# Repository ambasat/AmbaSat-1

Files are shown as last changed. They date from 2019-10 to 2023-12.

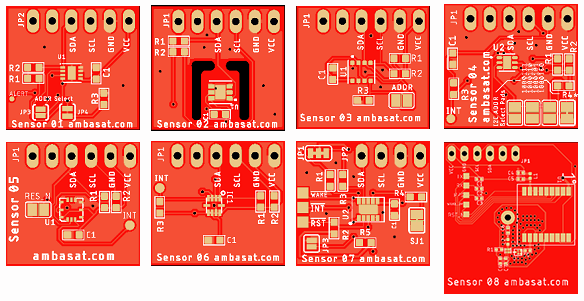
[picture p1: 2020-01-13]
Eagle/Daughterboards/AmbaSat-1-Sensor-range.png

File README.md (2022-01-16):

# AmbaSat-1

[Learn more at ambasat.com](https://ambasat.com)



AmbaSat-1 is tiny spacecraft kit that you assemble and code yourself.

Once your satellite kit is assembled and programmed, it will be launched onboard a commercial rocket which will deploy your satellite into Low Earth Orbit, where it will spend up to 3 months in space.

AmbaSat-1 is part of a new generation of satellites known as Sprite satellites. They are tiny spacecraft measuring 35 mm square and just a few millimetres thick. Pioneered by the original KickSat, groups of AmbaSat-1 satellites are launched onboard a commercial rocket. By shrinking the spacecraft, up to 200 satellites can be launched at a time, reducing costs.

Making use of The Things Network (TTN), AmbaSats are capable of transmitting data to over seven thousand earthbased TTN receivers (Gateways) which are spread around the whole globe. No specialist radio receiving equipment is required, your data appears over the internet directly to your AmbaSat Dashboard.

AmbaSats are just a little bigger than the size of a couple of postage stamps but have solar cells, a LoRaWAN radio transceiver, microcontroller (an Arduino compatible ATMEGA 328P-AU), memory, a gyroscope, accelerometer, magnetometer as well as a range of other sensor options. 

What’s in the AmbaSat Kit?

1. AmbaSat PCB – the main board where all the components are placed, including the MCU (Micro Controller Unit)
2. Micro Controller Unit – the brains of AmbaSat. This is where your code lives
3. Solar Panels – Spaceflight approved solar panels providing power to your satellite
4. Transceiver – The radio communications chip. This is the chip which will send data back to Earth and into your AmbaSat Dashboard
5. FTDI board – this is used for coding and converts your USB port to serial
6. Gyroscope, Accelerometer, Magnetometer – used to locate your satellite in space
7. A bag of parts containing resistors, capacitors, voltage regulator and other components
8. Your chosen sensor 

Software Coding (Programming the Satellite)

AmbaSat-1 is fully Arduino compatible and code is written using C/C++

Whether you’re new to the ‘C’ language or a seasoned pro, we have all the libraries, example source code and interfaces you need to get your satellite flying.

The AmbaSat kit comes complete with a FTDI USB adapter allowing direct coding in the Arduino IDE (based on C/C++). It’s the most popular programming environment for makers and hardware enthusiasts. 
AmbaSat is fully compatible with all Arduino related code examples. That’s because your satellite uses the well-respected Atmel ATMEGA-328 which is exactly the same microprocessor used by Arduino. In fact, your satellite is compatible with all online Arduino software libraries and your code will work with Arduino shields and modules with little or no library code modifications.

Never coded before? Don’t know the first thing about hardware?
That’s no problem. The AmbaSat Kit build will take you from learning how to use a soldering iron all the way through to assembling and coding your very own satellite. We’ve created a detailed step-by-step learning process:

Step 1. Unpacking your kit: What’s inside. The basics

Step 2. Electronics basics: Resistors, capacitors, MCU and other components

Step 3. Your toolbox: What you need. How to use it

Step 4. Assembly: The hardware and PCB. Putting it together

Step 5. Introduction to coding: Welcome to Arduino (C/C++). Let’s get your satellite coded

Step 6. Your AmbaSat Dashboard: Connecting to your Dashboard. Sending data from your satellite

What can I do with my satellite?
Measure! Explore! Measure!

What better way of showing off your uber-cool geekness than building your own spacecraft?

Your AmbaSat is fun but it’s also practical. Maybe you’re just looking to put your very own spacecraft into space. That’s great and also very cool. You can program it to send any message back to Earth that you like. However, if you’re looking for practical applications, including studying the environmental impact of gases, radiation, global warming, etc then read on!

Every AmbaSat comes loaded with a gyroscope, accelerometer and magnetometer sensor. These sensors come in the form of an integrated chip (IC) which is called the LSM9DS1. In low Earth orbit, there is no GPS signal available so this chip helps plot your satellite’s orbit in space. It’s a versatile, motion-sensing system-on-a-chip. It houses a 3-axis accelerometer, 3-axis gyroscope, and 3-axis
magnetometer – nine degrees of freedom (9DOF) in a single IC. See the LSM9DS1 overview section for more details on what this fantastic IC can do. In addition to the LSM9DS1, when you select your AmbaSat kit, you get the option to choose which type of additional sensor you would like to fit onto your satellite.

AmbaSat is Open Source
We’ve learned a lot from the open source community. Electronics, hardware, coding, software libraries and much more.

So, we want to give our work back to the maker and open source community.

The AmbaSat satellite software is fully open-source and available for full download. The AmbaSat satellite hardware is also totally open source and the schematics and Bill of Materials (BoM) are available for download.

What this means is that you can fully use all the above and create your own version of the AmbaSat satellite. Go ahead and use the schematic and source code and create your very own space satellite.

Come and join the journey at ambasat.com

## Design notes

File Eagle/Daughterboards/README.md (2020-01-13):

AmbaSat-1 sensors come on 'daughterboards' which you solder to the main AmbaSat-1 printed circuit board (PCB).

<!-- wp:heading -->
<h2>Available Sensor Options</h2>
<!-- /wp:heading -->

<!-- wp:paragraph -->
<p>There are eight sensors choices available, shown in the list below. One daughterboard sensor can fit on a single AmbaSat-1 mainboard.  </p>
<!-- /wp:paragraph -->

<h2>Sensor Boards</h2>



<!-- wp:paragraph -->
<p><strong>Sensor 01:    SHT30-DIS-F2.5KS  </strong></p>
<!-- /wp:paragraph -->

<!-- wp:paragraph -->
<p>Humidity and Temperature - Best in class Humidity &amp; Temperature Sensor. Fully calibrated, linearized, and temperature compensated digital output with a wide supply voltage range, I2C Interface with communication speeds up to 1MHz and two user selectable addresses.  Typical accuracy of 1.5 %RH and 0.1 °C. Very fast start-up and measurement time. All in a tiny 8-Pin DFN package.</p>
<!-- /wp:paragraph -->

<!-- wp:paragraph -->
<p><strong>Sensor 02    STS21   </strong></p>
<!-- /wp:paragraph -->

<!-- wp:paragraph -->
<p>Temperature - A 3x3mm, fully calibrated digital temperature sensor with impressive performance. The temperature sensor features a I²C address and comes with outstanding accuracy and low power consumption. </p>
<!-- /wp:paragraph -->

<!-- wp:paragraph -->
<p><strong>Sensor 03    BME680  </strong></p>
<!-- /wp:paragraph -->

<!-- wp:paragraph -->
<p>Gas, Pressure, Temp &amp; Humidity - a low power gas, pressure, temperature &amp; humidity sensor. It is a 4-in-1 multi-functional MEMS environmental sensor which integrates VOC (Volatile Organic Compounds) sensor, temperature sensor, humidity sensor and barometer. Monitor 4 environmental parameters simultaneously. Widely used in environmental monitoring, home automation and control, Internet of Things (IoT) wearable device, GPS, etc.</p>
<!-- /wp:paragraph -->

<!-- wp:paragraph -->
<p><strong>Sensor 04 OPT3001 DNPT  </strong>  </p>
<!-- /wp:paragraph -->

<!-- wp:paragraph -->
<p>Ambient Light Sensor - The OPT3001 is a sensor that measures the intensity of visible light. The spectral response of the sensor closely matches the photopic response of the human eye, with infrared rejection. It is a single-chip lux meter, measuring the intensity of light as visible by the human eye. The precision spectral response and strong IR rejection of the device enables the OPT3001 to accurately meter the intensity of light as seen by the human eye regardless of light source.</p>
<!-- /wp:paragraph -->

<!-- wp:paragraph -->
<p><strong>Sensor 05    ZMOD44 10AI1V   TVOC (Total Volatile Organic Compounds)</strong></p>
<!-- /wp:paragraph -->

<!-- wp:paragraph -->
<p>Designed for detecting total volatile organic compounds (TVOC). The ZMOD4410 is a 12-pin LGA assembly (3.0 x 3.0 x 0.7 mm) that consists of a gas sense element and a CMOS signal conditioning IC. The module’s sense element consists of heater element on a Si-based MEMS structure and a metal oxide (MOx) chemiresistor. The signal conditioner controls the sensor temperature and measures the MOx conductivity, which is a function of the gas concentration.</p>
<!-- /wp:paragraph -->

<!-- wp:paragraph -->
<p><strong>Sensor 06    SI1132-A10-GMR  UV Sensor </strong></p>
<!-- /wp:paragraph -->

<!-- wp:paragraph -->
<p>The Si1132 is a low-power, ultraviolet (UV) index, and ambient light sensor with I2C digital interface and programmable-event interrupt output. This sensor IC includes an analog-to-digital converter, integrated high sensitivity visible and infrared photodiodes, and digital signal processor. The Si1132 offers excellent performance under a wide dynamic range and a variety of light sources including direct sunlight.</p>
<!-- /wp:paragraph -->

<!-- wp:paragraph -->
<p><strong>Sensor 07    CCS811B-JOPD500 TVOC &amp; CO2 </strong></p>
<!-- /wp:paragraph -->

<!-- wp:paragraph -->
<p>The CCS811 is an ultra-low power digital gas sensor solution which integrates a metal oxide (MOX) gas sensor to detect a wide range of Volatile Organic Compounds (VOCs) and includes an Analog-to-Digital converter (ADC), and an I²C interface. Supporting intelligent algorithms to process raw sensor measurements and output equivalent total VOC (eTVOC) and<br> equivalent CO2 (eCO2) values.</p>
<!-- /wp:paragraph -->

<!-- wp:paragraph -->
<p><strong>Sensor 08    TESEO-LIV3R*    GPS </strong></p>
<!-- /wp:paragraph -->

<!-- wp:paragraph -->
<p>The Teseo-LIV3R module is an easy to use Global Navigation Satellite System (GNSS) standalone positioning receiver IC working simultaneously on multiple constellations. This certified module comes with optimized RF, embedded firmware and is compact at only 9.7x10.1 mm. Supporting GPS, Glonass, BeiDou &amp; QZSS positioning systems.</p>
<!-- /wp:paragraph -->

<!-- wp:paragraph -->
<p><em>*Please note: Due to COCOM restrictions, the </em><em>TESEO GPS receiver will only work on Earth</em></p>
<!-- /wp:paragraph -->

<!-- wp:heading -->
<h2>Datasheets</h2>
<!-- /wp:heading -->

<!-- wp:paragraph -->
<p>Datasheets for each of the above sensors can be download
from the links at:</p>
<!-- /wp:paragraph -->

<!-- wp:heading -->
<h2><a href="https://ambasat.com/ambasat-2/sensor-options/">https://ambasat.com/ambasat-2/sensor-options/</a>&nbsp;</h2>
<!-- /wp:heading -->

<!-- wp:heading -->
<h2>Custom sensors</h2>
<!-- /wp:heading -->

<!-- wp:paragraph -->
<p>You can create a custom sensor as long as it conforms to
certain criteria, including size and safety. Your AmbaSat satellite provides
additional connectivity pins which expose the ATMEGA's I2C bus, as well as
digital and analogue pins, plus power. Please contact <a href="mailto:custom@ambasat.com">custom@ambasat.com</a> for more details.</p>
<!-- /wp:paragraph -->

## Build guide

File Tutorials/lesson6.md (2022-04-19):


## Introduction
Okay, you have got your Ambasat-1 board set up and also figured out how to transmit programs to the board using VSCode. Good job!

However... just running example programs is a bit boring. Let's do something more interesting; in this lesson, you will learn to use your imagination and create your very first satellite firmware.

## Requirements
 -  Ambasat-1 Satellite
 Ambasat-1 (https://ambasat.com/wp-content/uploads/2020/06/AmbaSat-1-Assembled-350.jpg "Ambasat-1")
 - USB programmer
 

In case you haven't set up your coding environment yet, you can complete this tutorial using the [Arduino Online Simulator](https://wokwi.com/projects/new/arduino-unohttp:// "Arduino Online Simulator")

## What is a program?

A program is a set of instructions that a computer follows in order to perform a particular task. There are multiple languages available to developers, each one of them is suited for specific applications. In the embedded field the most common languages used are C and C++. Other languages you may have heard of are **Python**, **Java**,, or **C#**. 

An Ambasat-1 source code or also called sketch( because of the Arduino framework) is composed of two main parts: setup code and a loop code.

### Setup  
- Executed immediately after power-up or reboot.
- It is where all the initializing code must be put, e.g., variables, pin modes, or libraries.

### Loop
- Executed after the setup function.
- Executed repeatedly, that is why the name 'Loop.'
- It is where the main task of the program gets executed.

### Example
```c
#include <Arduino.h>

// put your setup code here, to run once:
void setup() {
  Serial.begin(9800); // Initialize the Serial comunication, 9800 is the baudrate
  Serial.println("Setup code"); // Print the massage through the serial line
}

// put your main code here, to run repeatedly:
void loop() {
  Serial.println("loop code");
}
```
Let's try it yourself, copy and paste this code on  https://wokwi.com/projects/new/arduino-uno. Then, click the run button to start the simulation. What is the output?

As you can see, the line "Setup code" is printed only once at the begging. On the other hand, the line "loop code" is printed several times. Be aware that both functions setup() and loop() **MUST** be included in every program you write.

You have probably  noticed that the code has differen coloring and shading. These hints makes the code more easy to read and understand. Let's have a look at the main parts of the program.

To include a library, we use the keyword: `#include` followed by `<nameofthelibrary.h>`. In the example, we wrote `#include <Arduino.h>` to import the Arduino framework. Ignore for now what a framework is. Just think of it as the underlying layer that does the dirty work for us.

Notice that there are some plain English sentences in the code; those are called comments. We use comments to describe what the code is doing so that the other developers can understand more easily our code. We use a double slash followed by the comment itself to create a comment in C/C++.

    //This is a comment!

**Setup** and **Loop** are commonly called functions. You can think of functions as a collection of statements. We use a function to group statements together so that we can dynamically refer to them without having to rewrite them every time. Picture a function as a to-do list or a list of procedures that are executed in order.

    // put your main code here, to run repeatedly:
    void loop() {
      Serial.println("loop code");
    }
This one is a bit more complicated example. It looks scary, doesn't it? A function can optionally receive input values. In this case, *mysterious_fun* requires two numbers, **x** and **y**. Can you guess what the function does with these two parameters?

    void mysterious_fun( int x, int y)
    {
    	Serial.println(x+y);
    }

Try to execute the following code, what does it print?
    #include <Arduino.h>
    
    void setup() {
      // put your setup code here, to run once:
      Serial.begin(9800); // Initialize the Serial comunication, 9800 is the baudrate
      Serial.println("Setup code"); // Print the massage through the serial line
    }
    
    void loop() {
      // put your main code here, to run repeatedly:
      Serial.println("Hello");
      sum(5,2);
    }
    
    void mysterious_fun(int x, int y)
    {
      Serial.println(x+y);
    }

At this point, you might be asking yourself, "what is void?" Well, that is a fancy way of saying **nothing**. Technically it means that the function doesn't return anything. This implies that we can write a function that returns something, but that is a lesson for another day.
### Quiz Time

It is time to test what you have learned so far! (Don't worry, you won't be graded)

#### What is this line of code:
        // put your setup code here, to run once:
1. A keyword
2. A single line comment
3. A function definition
4. A cup of tea

#### What is this line of code 2:
    void loop() {
    	Serial.println("Hello Students!");
    }
1.  A statement
2.  A single line comment
3.  A function definition
4.  A banana

## Light the board up

Ok, now that you have a better understanding of what a program is, let's experiment with something more practical. In the following example, we are going to make our first LED blink! Don't worry, you don't need anything else than your Ambasat board. However, you can always spice things up and use an external Led along with the appropriate resistor.

### About LED
A light-emitting diode is an electronic component that emits light when current flows through it. It has two pins:
- Cathode (- pin) needs to be connected to GND (0V).
- Anode (+pin) is used to control LED status.

For most LEDS we must use a resistor to protect the LED. We place a resistor between the Anode (+) and the VCC(+5V). The value of the resistor depends on the specification of the LED. To control the status of the LED we connect the anode(+) to a digital pin so that we can dynamically change the pin output.

(https://i.ibb.co/sRKDYrF/Screenshot-2022-02-27-at-19-48-05.pnghttp://)
### Write the code
First, we must decide which digital pin we are going to use. For simplicity let's stick with the Ambasat onboard status LED which is connected to digital pin 9.
```c
#define INTERNAL_LED 9
```

Secondly, we must configure the pin status. There are two possible configurations; Input in case we are interested in reading the pin voltage; Output in case we are interested in controlling the pin output voltage. Obviously, we are interested in the latter, so we configure the INTERNAL_LED as Output:
```c
pinMode(INTERNAL_LED, OUTPUT);

```
Lastly, to control the LED status we use the following command
```c
digitalWrite(INTERNAL_LED, High or Low);
```
The following is an example of the LED blinking, try it yourself!
```c
#define LED 13

// put your setup code here, to run once
void setup() {
  // initialize digital pin LED as an output.
  pinMode(LED, OUTPUT);
}

// put your main code here, to run repeatedly:
void loop() {
  // turn the LED on (HIGH is the voltage level)
  digitalWrite(LED, HIGH);
  // wait for 1 second
  delay(1000);
  // turn the LED off by making the voltage LOW
  digitalWrite(LED, LOW);
  // wait for 1 second
  delay(1000);
}
```

 Now get you hands dirty, try to change the delay, what happened?
### Quiz Time 2
#### What does this line of code do:
       digitalWrite(LED, HIGH);
1. Digital write something
2. Turn the LED off
3. Reset the board 
4. Turn the LED on

#### What does this line of code do:
    delay(1000);
1.  Wait for 1000ms (1 second)
2.  Turn the LED on
3.  Write "hello" into the serial output
4.  Reset the board

### Exercise
Time to test your knowledge with some practical exercises! Try to complete as many as you can.

#### Change the example code so that the light is on for 500 milliseconds and off for 500 milliseconds. 

#### Change the example code so that the light is on for 50 milliseconds and off for 50 milliseconds. What happens?

#### Build a simple LED circuit and try to make this LED blink instead of the internal one. What line of code do you need to change?

#### Using the example code as a starting point, build a Blink SOS signal in Morse code.	
Tips:
- Morse code Alphabet is composed of just two basic signals - dots and dashes. The dot represents a quick and rapid signal. Dashes, on the other hand, represent a slow signal.
- SOS in Morse code is 3 dots - 3 dashes - 3 dots.
- How can we differentiate between dots and dashes with a LED? In a very simple way, by changing the time spent blinking.
- As general rule dashes should be three times longer than the dots.
- The timing between dots and dashes should be the length of a dot.
- To make the signal more clear, the pause between letters should be the same length as your dash blinks.

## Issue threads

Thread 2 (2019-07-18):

4Mhz Fuse Values

C4, 2019-07-18:
Hi, I was wondering what fuse values you were using to for the Atmega32P-AU chips before you install them on the boards? This would be nice to know for others that are building ambasat boards. Thanks!

ambasat, 2020-01-27:
Hi, here are the fuse values for 1MHz:

ambasatnode.menu.mhz.1MHz.bootloader.low_fuses=0x62
ambasatnode.bootloader.high_fuses=0xD6
ambasatnode.bootloader.extended_fuses=0x06

For 4MHz, change:

ambasatnode.menu.mhz.4MHz.bootloader.low_fuses=0x7D

Closed 2020-01-27.

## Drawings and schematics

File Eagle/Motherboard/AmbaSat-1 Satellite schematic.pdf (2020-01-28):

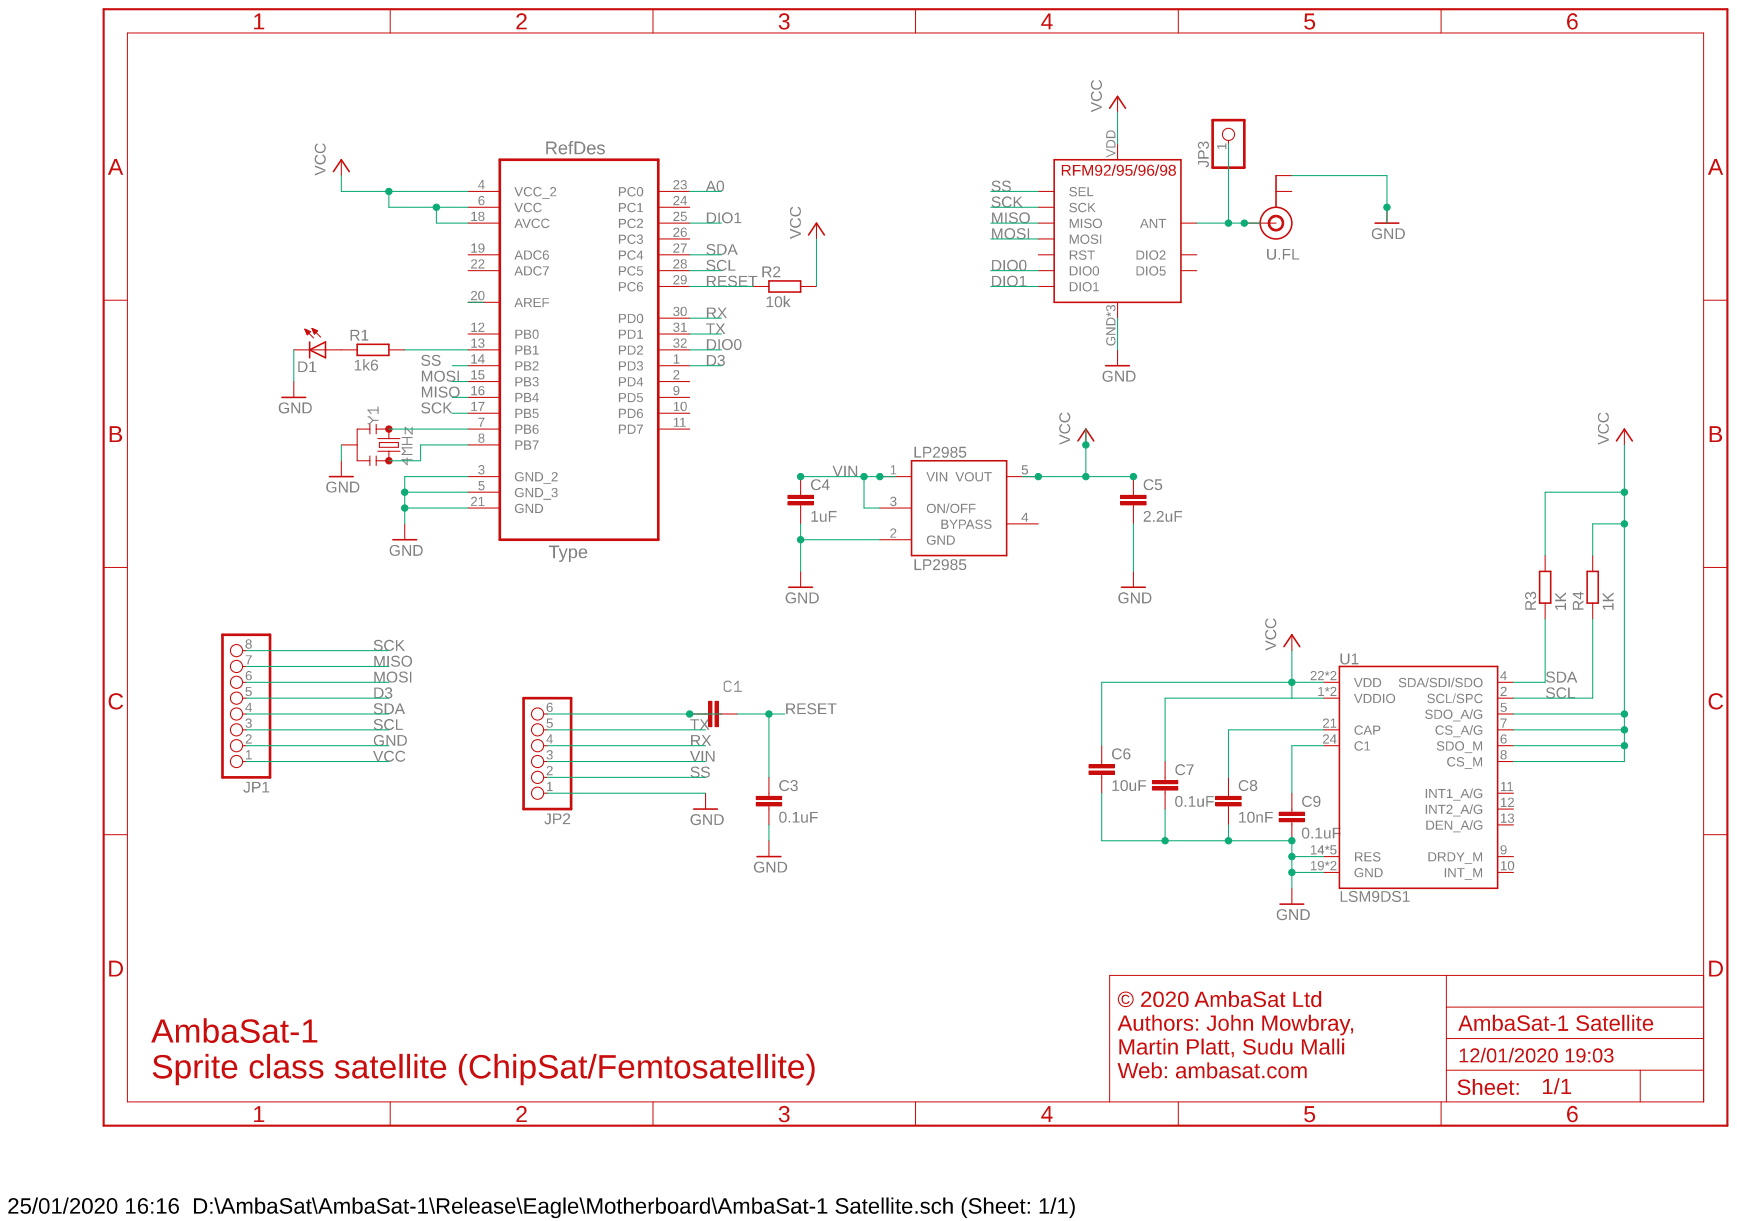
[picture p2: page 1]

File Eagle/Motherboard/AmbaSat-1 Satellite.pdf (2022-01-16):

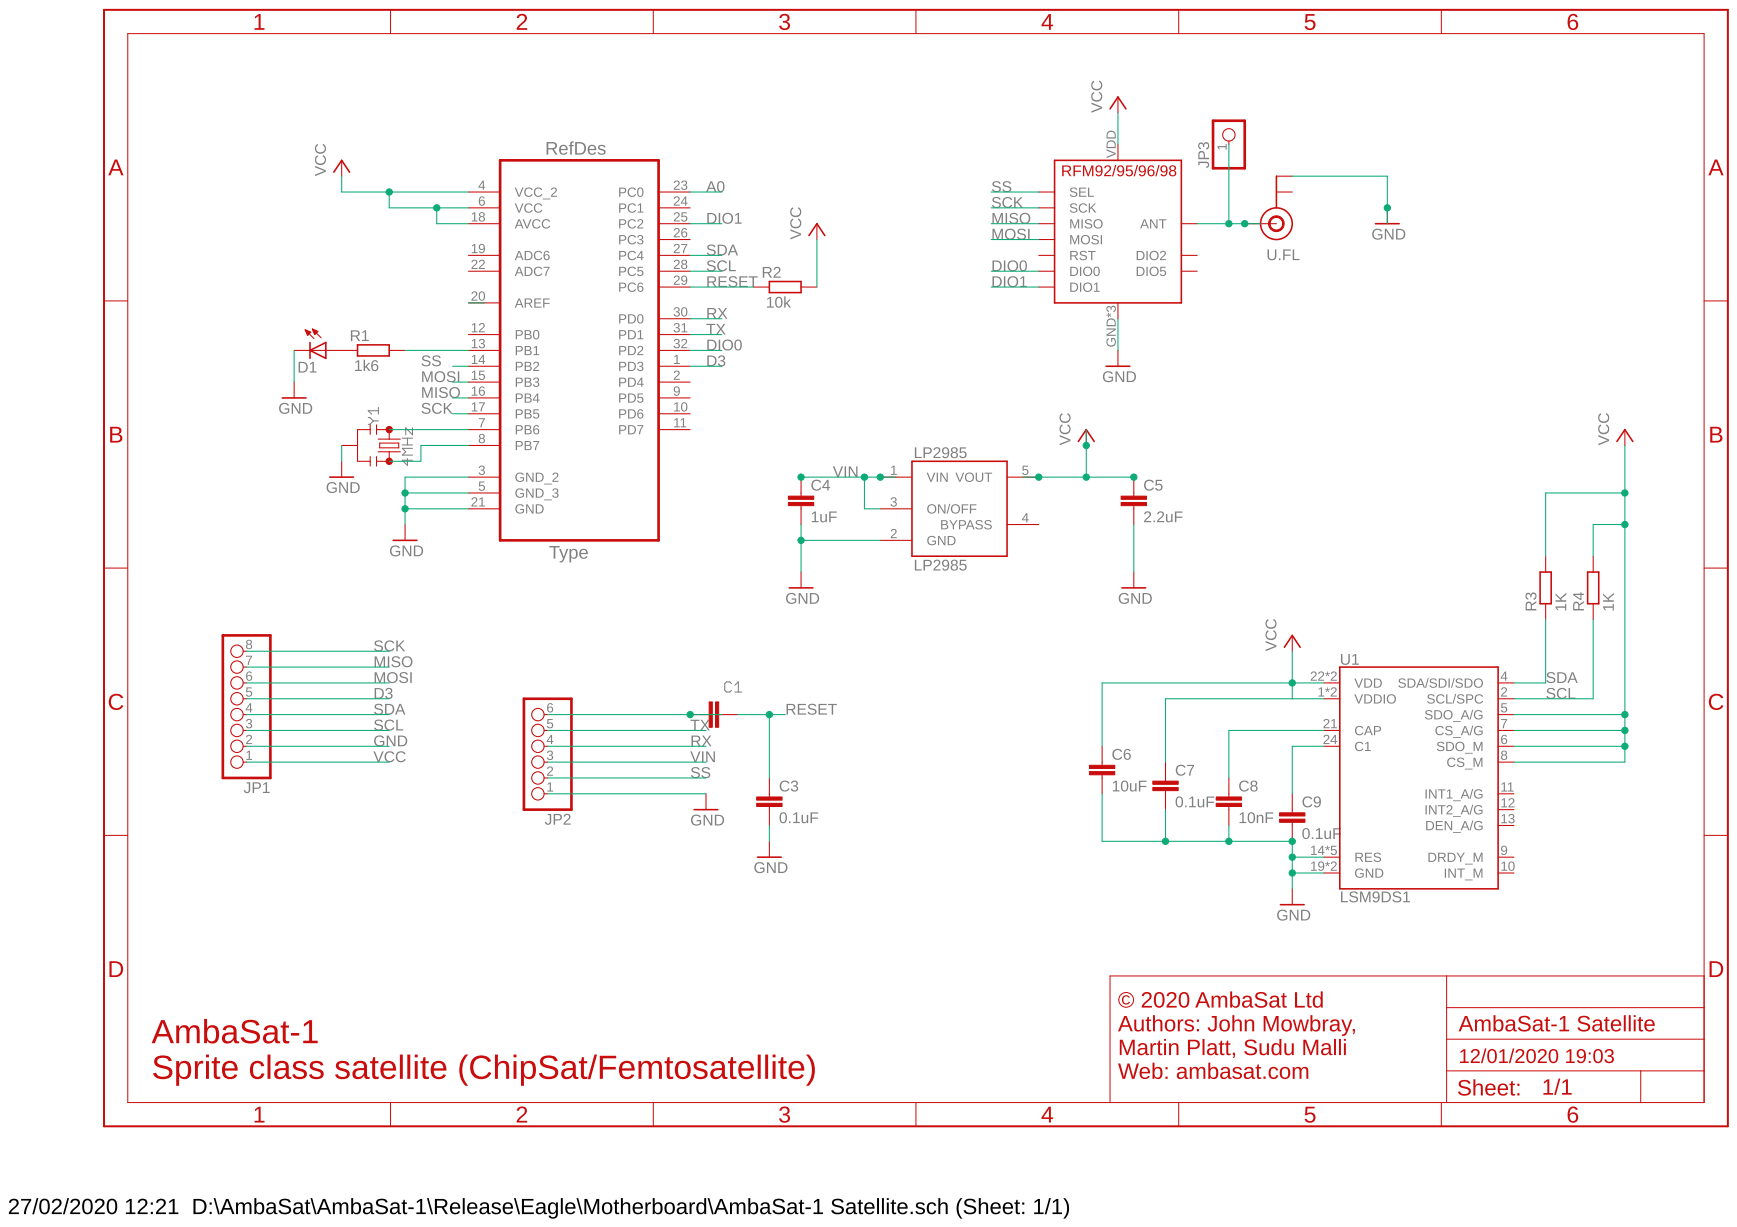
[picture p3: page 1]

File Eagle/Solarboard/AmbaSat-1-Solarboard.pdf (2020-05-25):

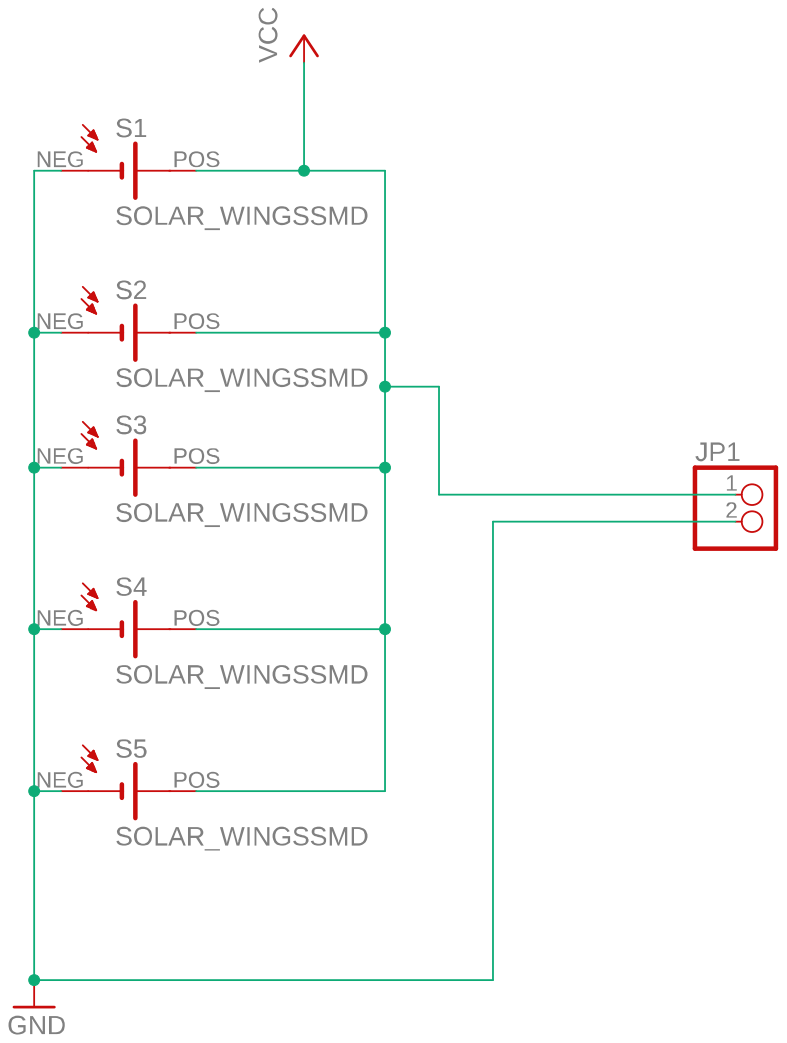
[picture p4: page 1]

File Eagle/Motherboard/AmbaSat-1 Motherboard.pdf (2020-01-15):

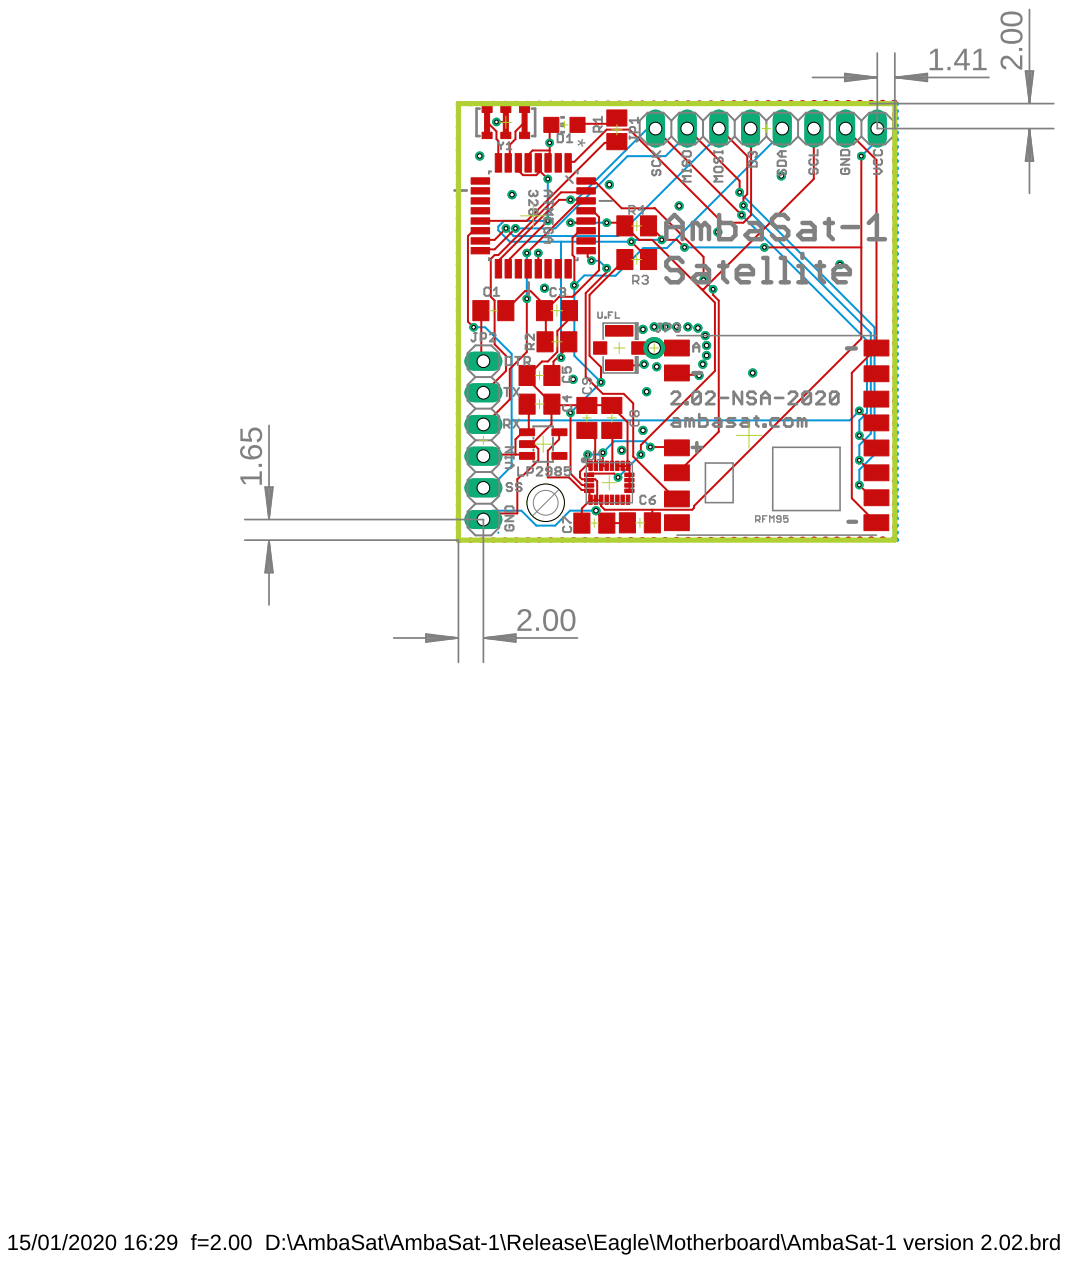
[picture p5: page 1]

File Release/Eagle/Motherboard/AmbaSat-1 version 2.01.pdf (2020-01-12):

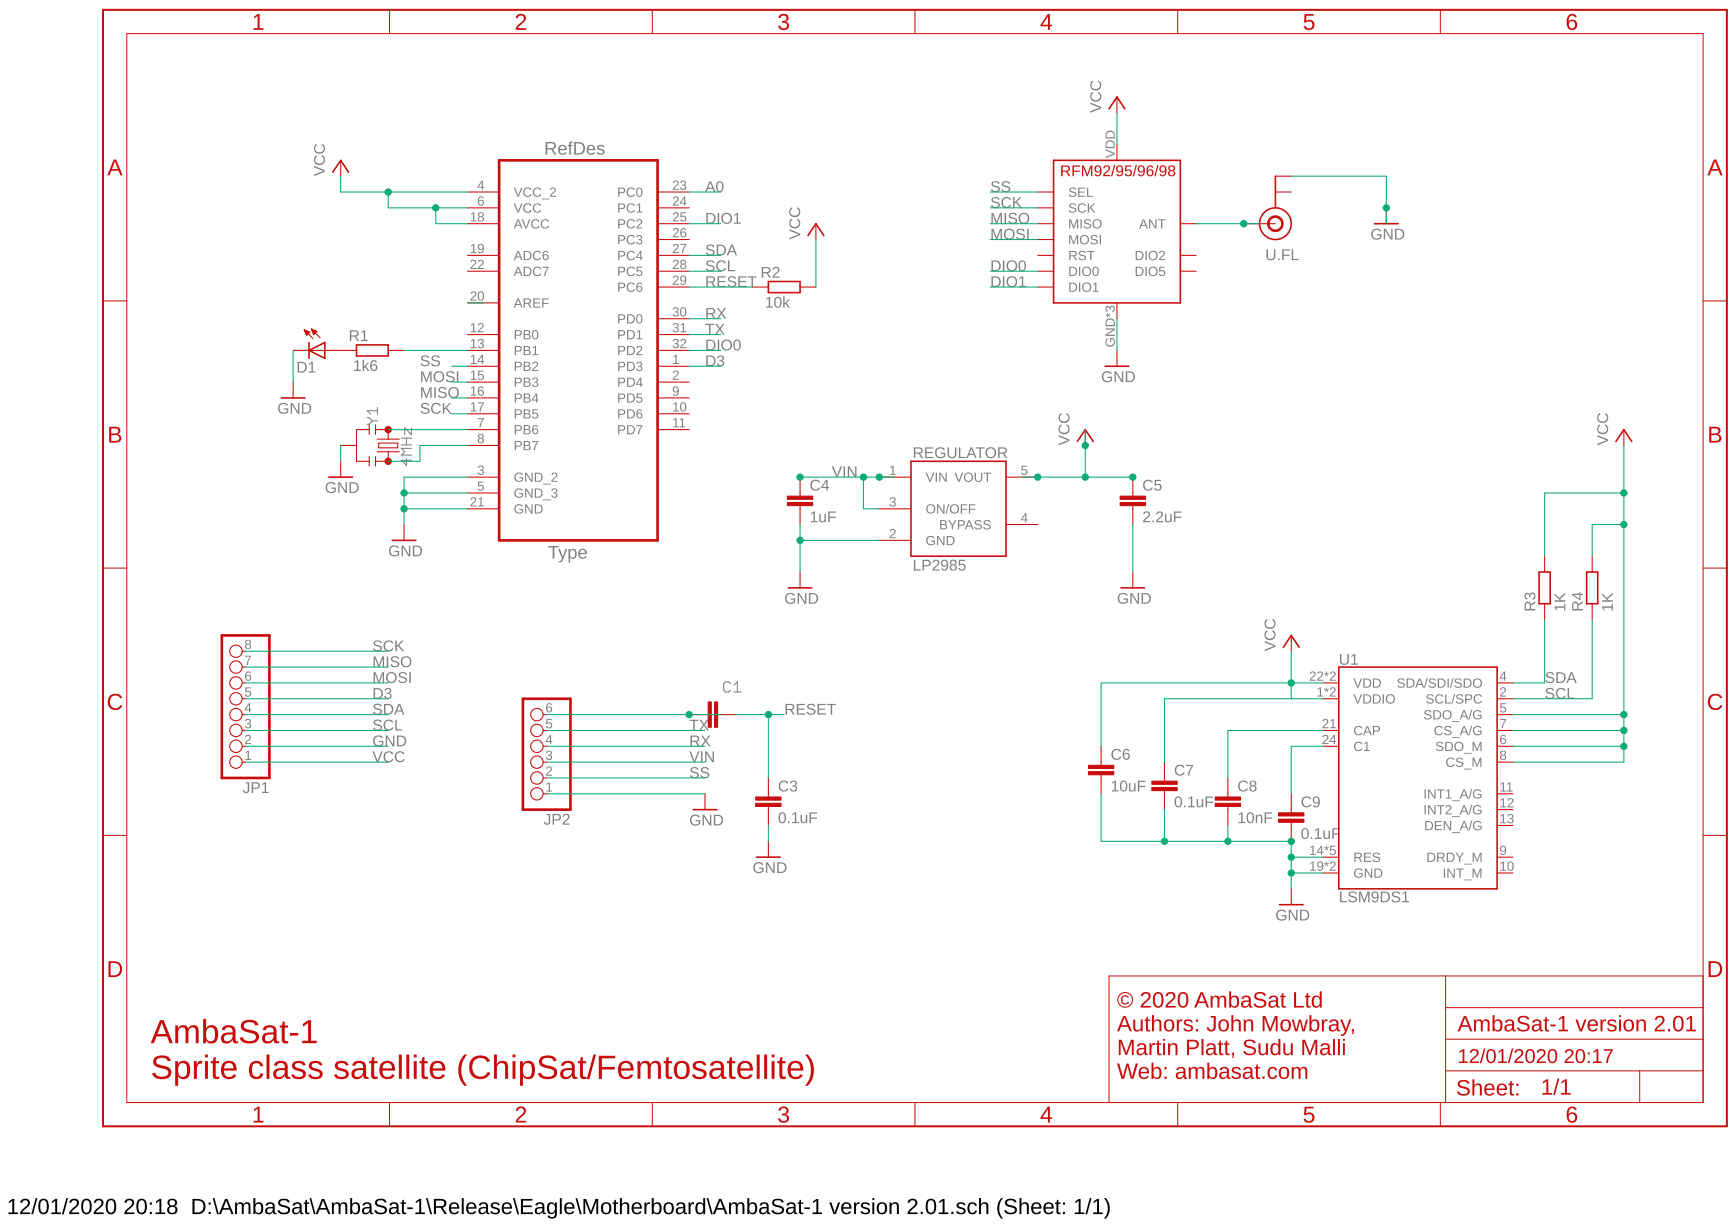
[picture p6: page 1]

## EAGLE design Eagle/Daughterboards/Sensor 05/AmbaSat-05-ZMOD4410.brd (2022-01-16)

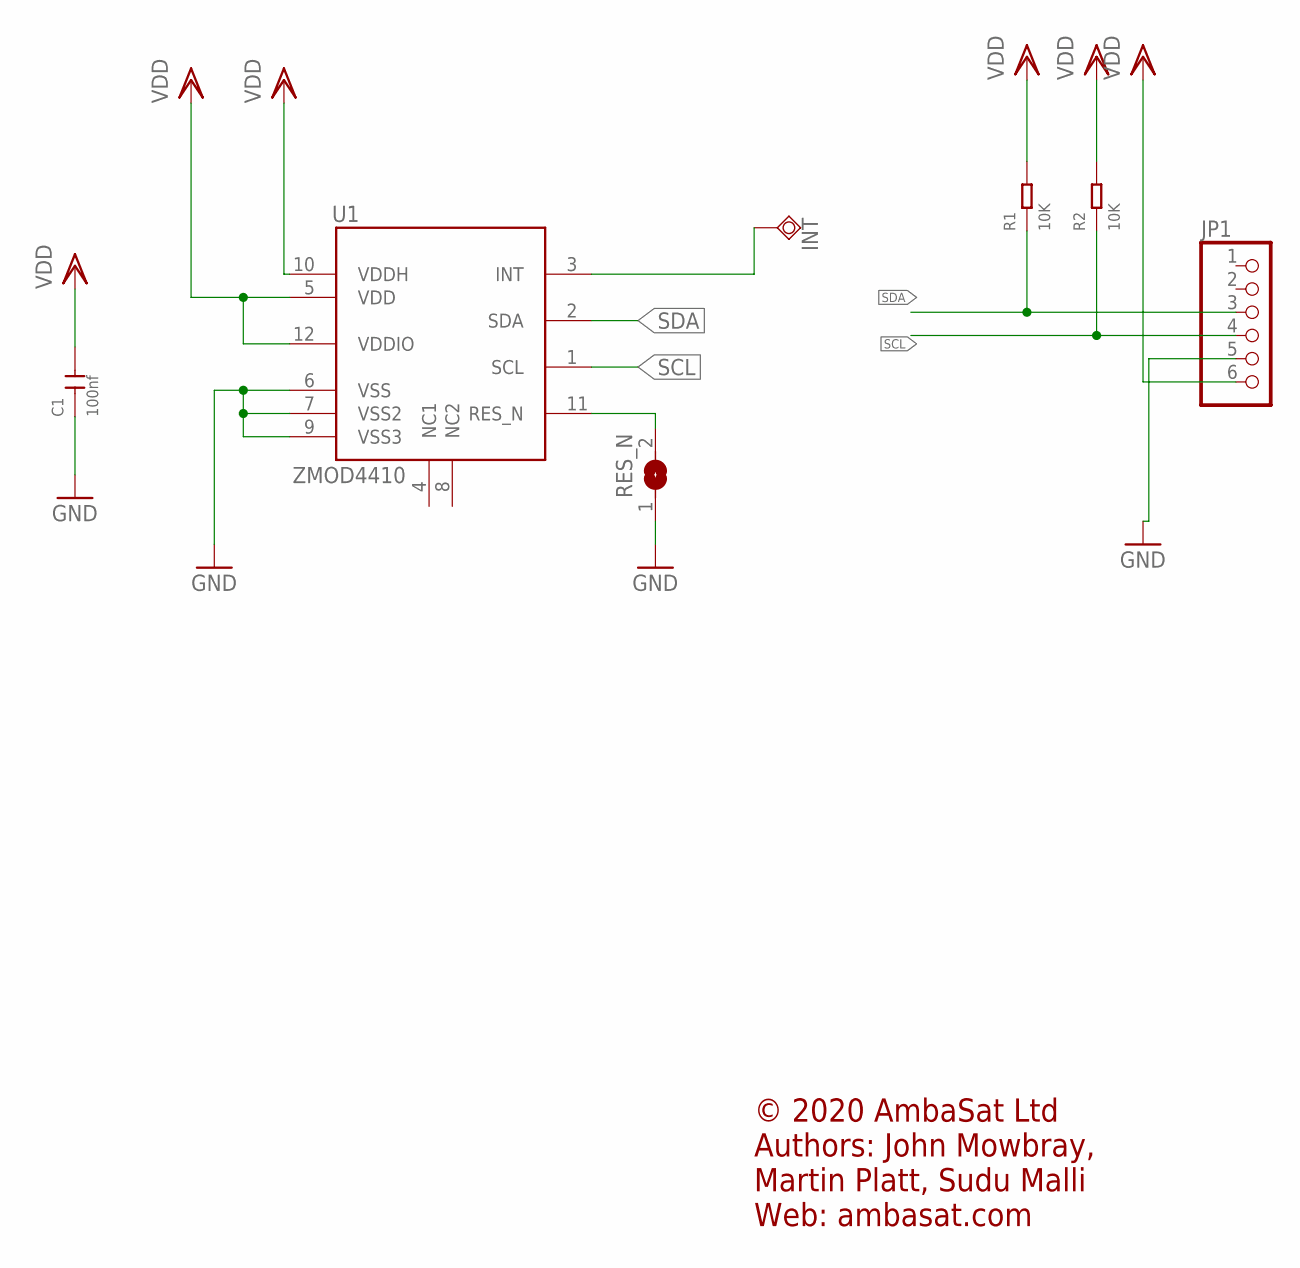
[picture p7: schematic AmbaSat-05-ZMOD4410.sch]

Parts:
C1: 100nf; C0805
INT: TESTPAD_TPSQTP12R; TESTPAD_TP12R
JP1: HEADER-1X6; 1X06_OVAL
R1, R2: 10K; R0805
RES_N: SJ
U1: ZMOD4410; LGG12D1_3X3X0.7_0.5X1

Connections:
GND: C1.1, JP1.5, RES_N.1, U1.6 (VSS), U1.7 (VSS2), U1.9 (VSS3)
unnamed: INT.TP, U1.3 (INT)
unnamed: RES_N.2, U1.11 (RES_N)
SCL: JP1.4, R2.1, U1.1 (SCL)
SDA: JP1.3, R1.1, U1.2 (SDA)
VDD: C1.2, JP1.6, R1.2, R2.2, U1.5 (VDD), U1.10 (VDDH), U1.12 (VDDIO)

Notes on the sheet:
© 2020 AmbaSat Ltd Authors: John Mowbray, Martin Platt, Sudu Malli Web: ambasat.com

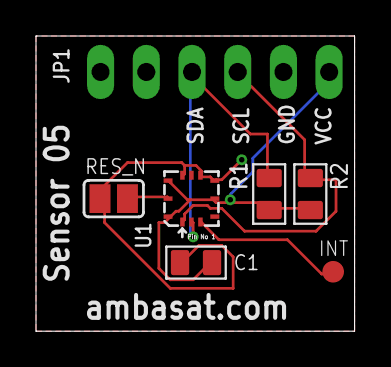
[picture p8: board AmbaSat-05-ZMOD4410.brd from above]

Board: 2 copper layers, 17.7 x 16.4 mm, 7 parts (0 on the bottom side), 6 nets.

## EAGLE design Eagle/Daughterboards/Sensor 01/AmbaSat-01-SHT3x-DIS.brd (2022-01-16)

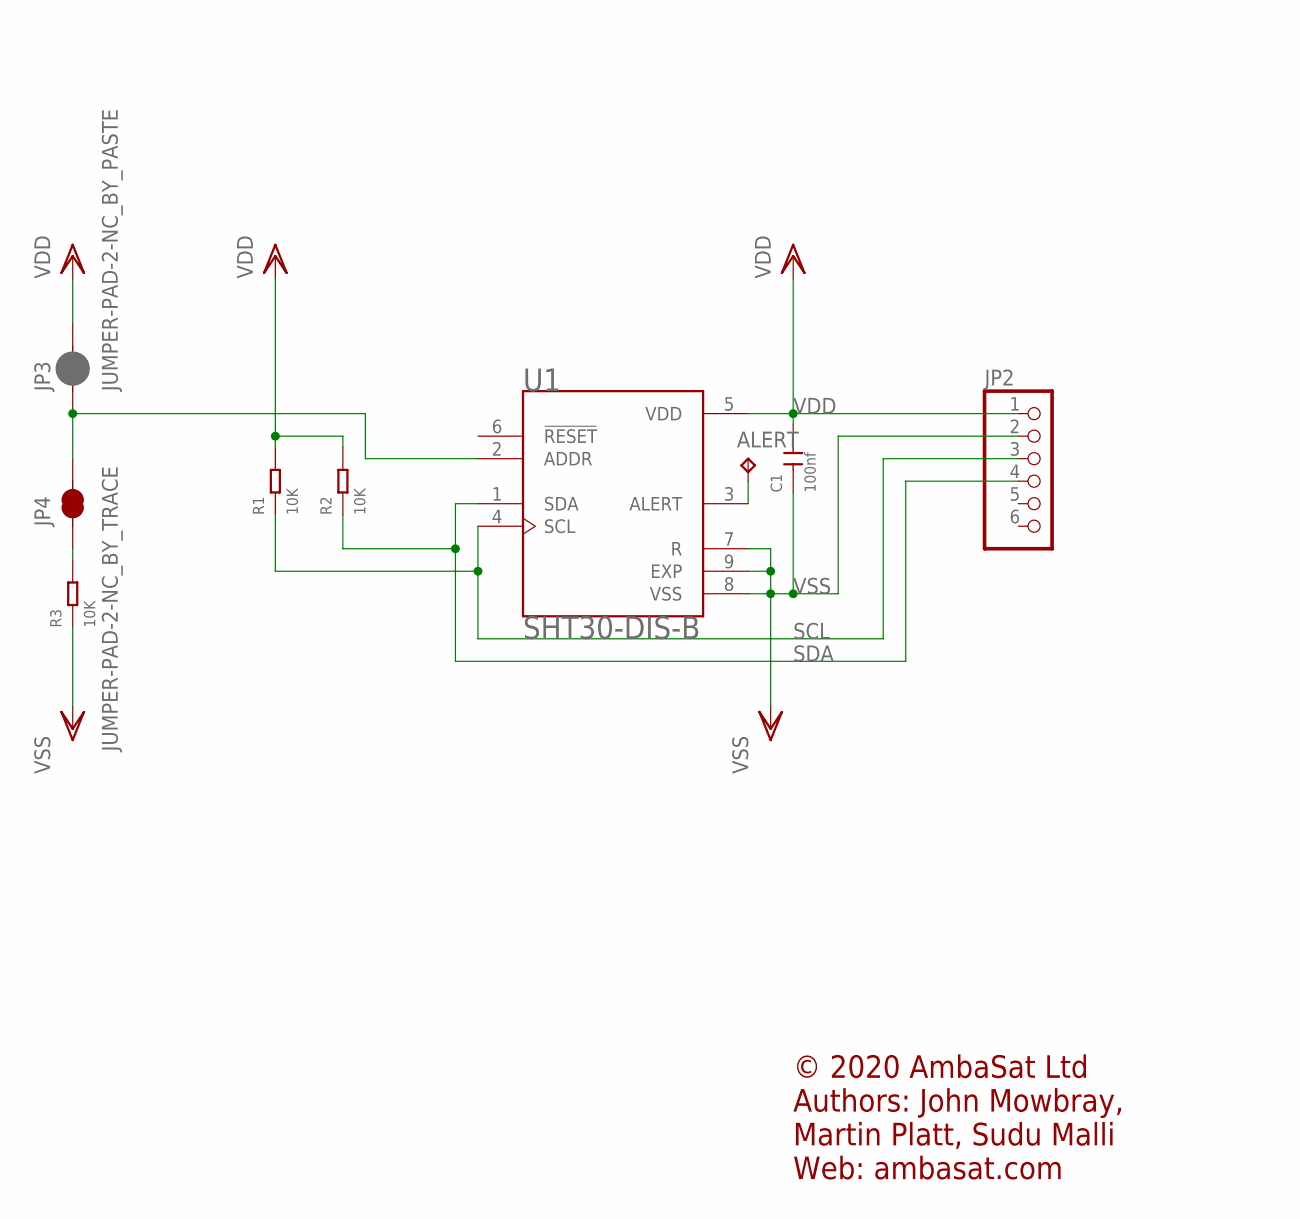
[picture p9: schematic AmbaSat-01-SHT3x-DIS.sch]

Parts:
ALERT: TPTP06R; TP06R
C1: 100nf; C0805
JP2: HEADER-1X6; 1X06_OVAL
JP3: JUMPER-PAD-2-NC_BY_PASTE; PAD-JUMPER-2-NC_BY_PASTE_YES_SILK
JP4: JUMPER-PAD-2-NC_BY_TRACE; PAD-JUMPER-2-NC_BY_TRACE_YES_SILK
R1, R2, R3: 10K; R0805
U1: SHT30-DIS-B; DFN250X250X100-9N

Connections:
unnamed: JP3.1, JP4.2, U1.2 (ADDR)
unnamed: ALERT.TP, U1.3 (ALERT)
unnamed: JP4.1, R3.2
SCL: JP2.3, R1.1, U1.4 (SCL)
SDA: JP2.4, R2.1, U1.1 (SDA)
VDD: C1.2, JP2.1, JP3.2, R1.2, R2.2, U1.5 (VDD)
VSS: C1.1, JP2.2, R3.1, U1.7 (R), U1.8 (VSS), U1.9 (EXP)

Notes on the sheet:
© 2020 AmbaSat Ltd Authors: John Mowbray, Martin Platt, Sudu Malli Web: ambasat.com

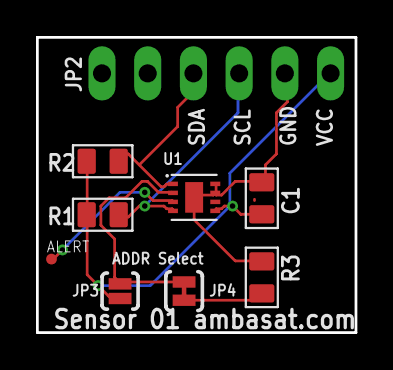
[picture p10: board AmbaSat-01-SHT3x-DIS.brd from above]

Board: 2 copper layers, 17.7 x 16.4 mm, 9 parts (0 on the bottom side), 7 nets.

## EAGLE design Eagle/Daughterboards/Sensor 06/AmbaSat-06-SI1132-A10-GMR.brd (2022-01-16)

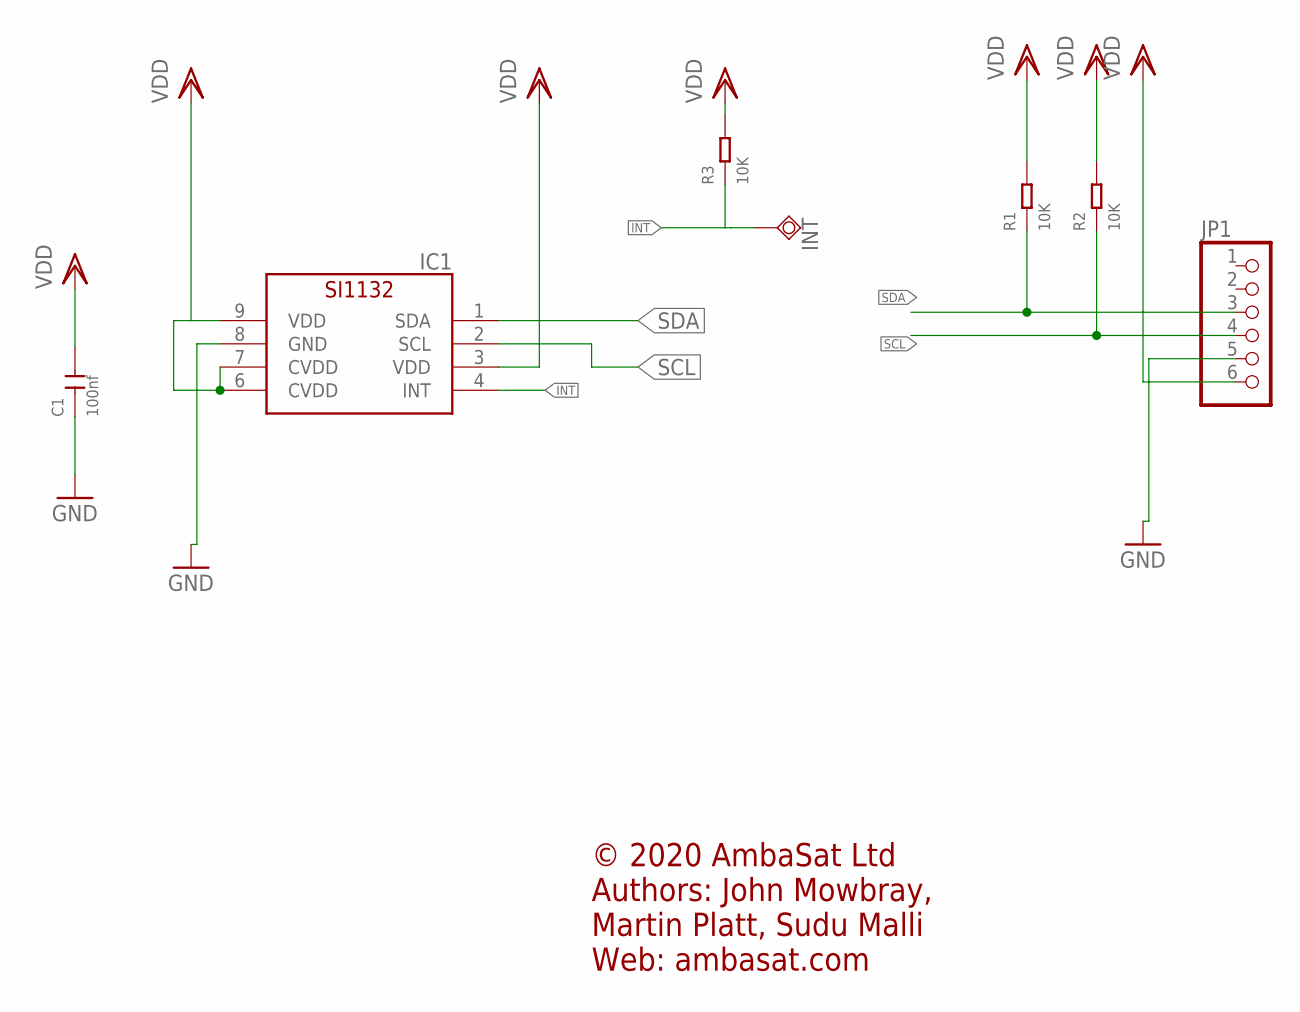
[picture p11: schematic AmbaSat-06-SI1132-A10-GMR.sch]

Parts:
C1: 100nf; C0805
IC1: SL-SI1132; SILICONLABS-SI1132
INT: TESTPAD_TPSQTP12R; TESTPAD_TP12R
JP1: HEADER-1X6; 1X06_OVAL
R1, R2, R3: 10K; R0805

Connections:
GND: C1.1, IC1.8 (GND), JP1.5
INT: IC1.4 (INT), INT.TP, R3.1
SCL: IC1.2 (SCL), JP1.4, R2.1
SDA: IC1.1 (SDA), JP1.3, R1.1
VDD: C1.2, IC1.3 (VDD), IC1.6 (CVDD), IC1.7 (CVDD), IC1.9 (VDD), JP1.6, R1.2, R2.2, R3.2

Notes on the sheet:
© 2020 AmbaSat Ltd Authors: John Mowbray, Martin Platt, Sudu Malli Web: ambasat.com

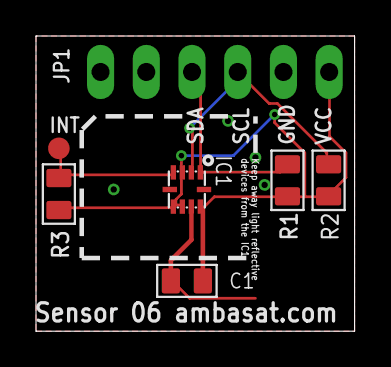
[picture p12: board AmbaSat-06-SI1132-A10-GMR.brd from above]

Board: 2 copper layers, 17.7 x 16.4 mm, 7 parts (0 on the bottom side), 5 nets.

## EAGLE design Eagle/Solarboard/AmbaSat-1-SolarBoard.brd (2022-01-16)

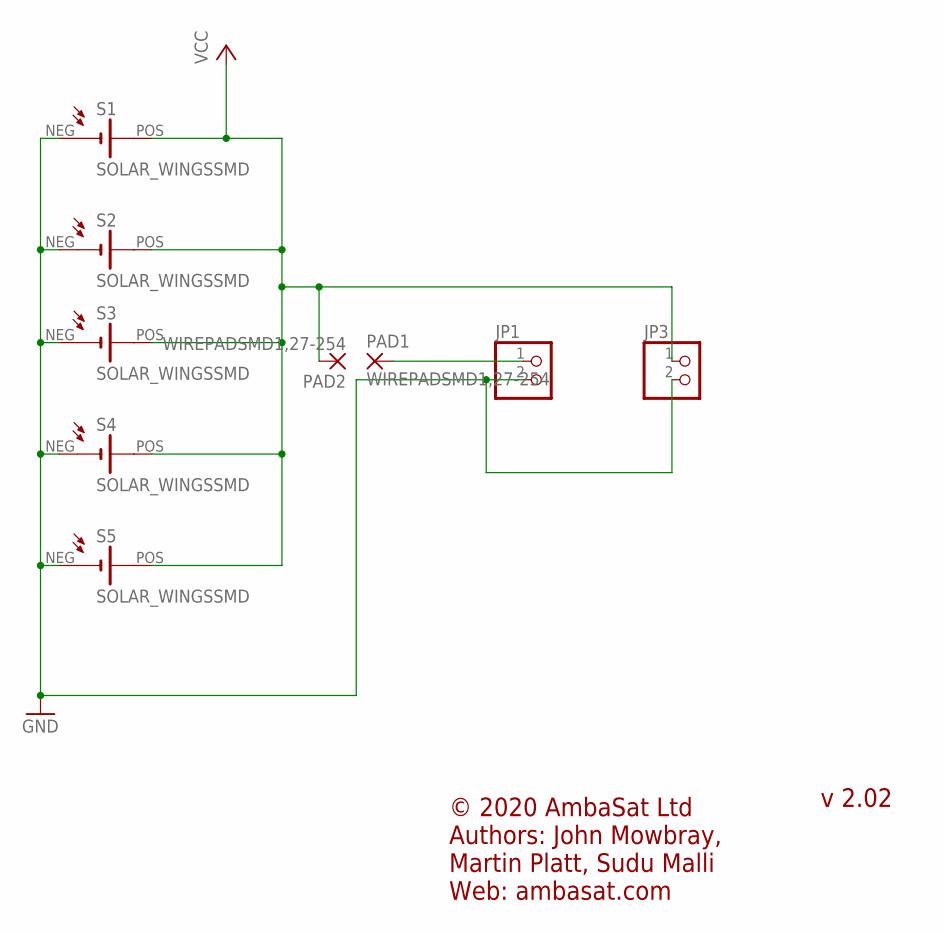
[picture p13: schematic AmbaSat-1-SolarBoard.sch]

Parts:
JP1, JP3: PINHD-1X2; 1X02
PAD1, PAD2: WIREPADSMD1,27-254; SMD1,27-2,54
S1, S2, S3, S4, S5: SOLAR_WINGSSMD; SOLAR_WINGS_SMD

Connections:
GND: JP1.2, JP3.2, S1.NEG, S2.NEG, S3.NEG, S4.NEG, S5.NEG
unnamed: JP1.1, PAD1.1
VCC: JP3.1, PAD2.1, S1.POS, S2.POS, S3.POS, S4.POS, S5.POS

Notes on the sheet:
© 2020 AmbaSat Ltd Authors: John Mowbray, Martin Platt, Sudu Malli Web: ambasat.com
v 2.02

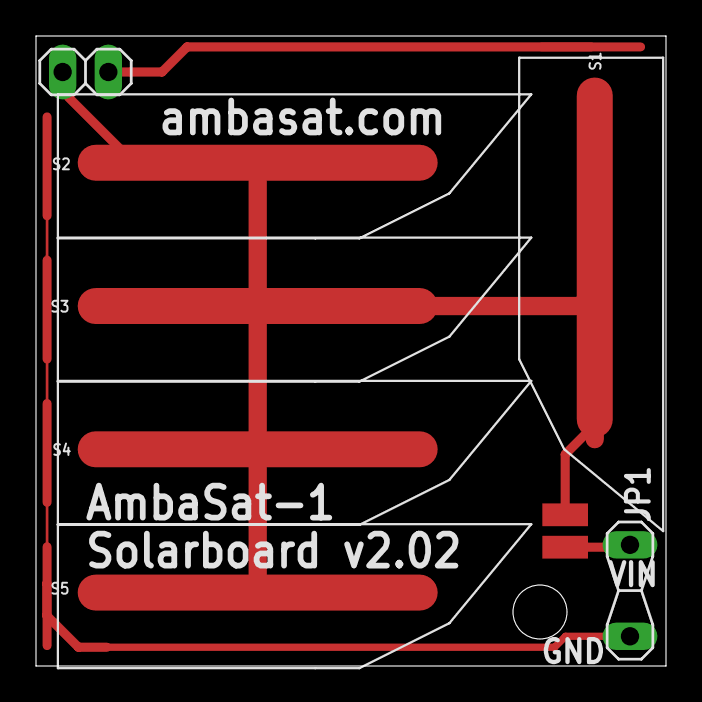
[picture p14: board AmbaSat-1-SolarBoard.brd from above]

Board: 2 copper layers, 35.0 x 35.0 mm, 9 parts (0 on the bottom side), 3 nets.

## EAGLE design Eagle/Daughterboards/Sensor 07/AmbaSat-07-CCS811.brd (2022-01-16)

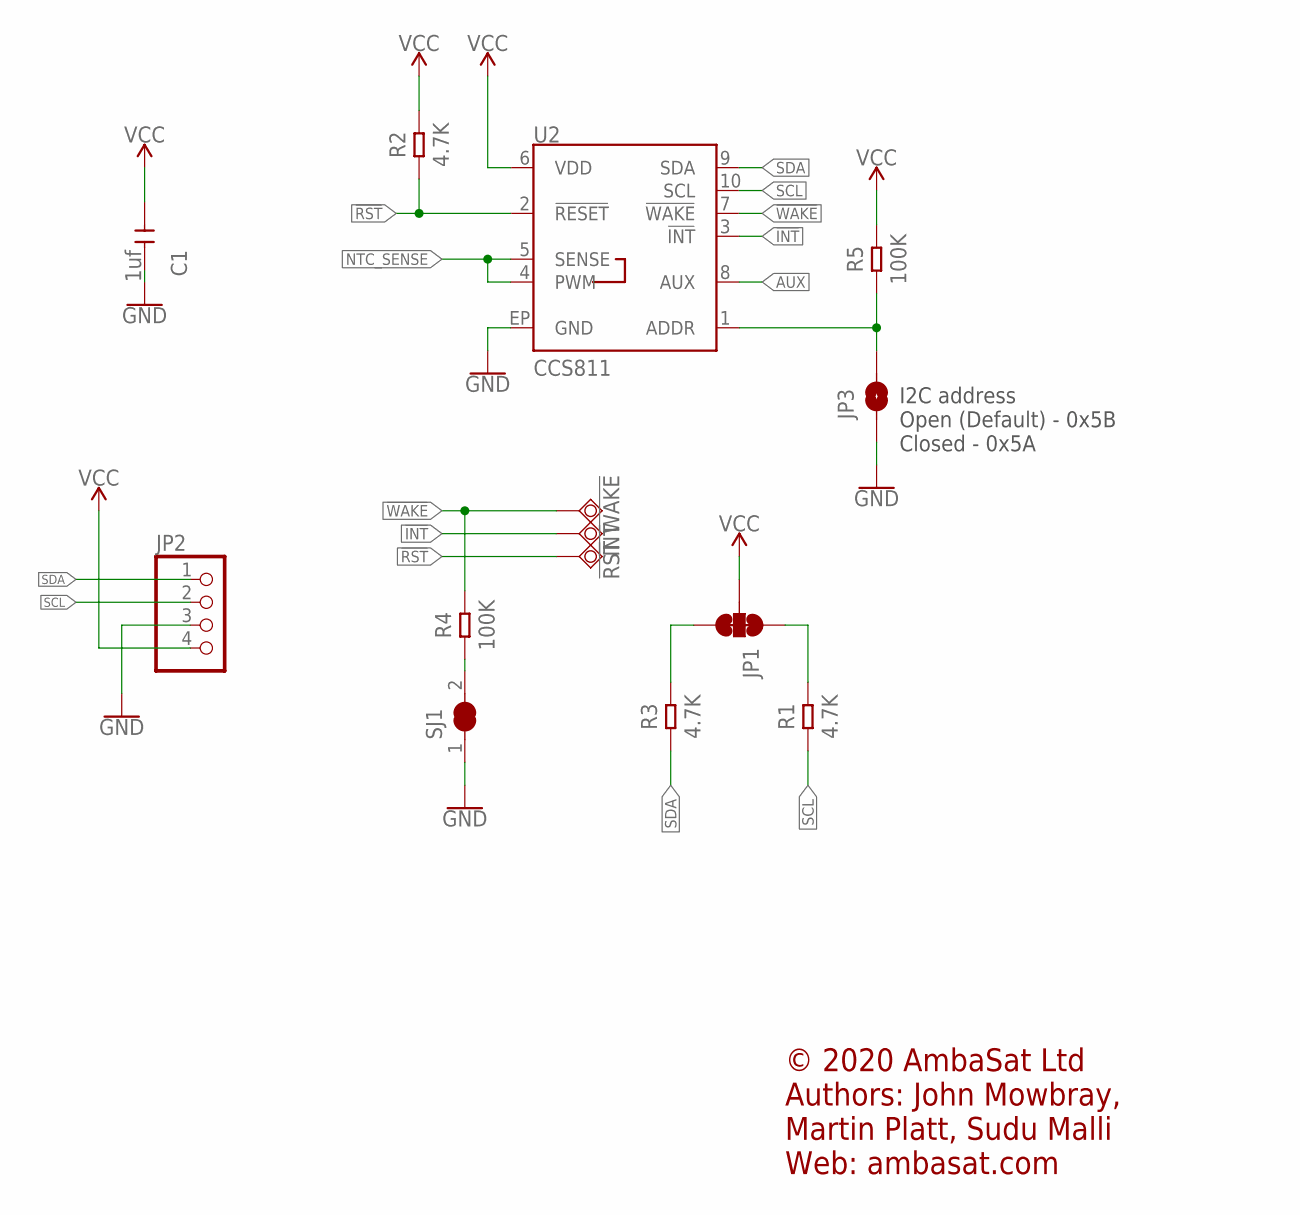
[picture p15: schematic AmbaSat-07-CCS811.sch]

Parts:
!INT: TESTPAD_TPSQTP14SQ; TESTPAD_TP14SQ
!RST: TESTPAD_TPSQTP14SQ; TESTPAD_TP14SQ
!WAKE: TESTPAD_TPSQTP14SQ; TESTPAD_TP14SQ
C1: 1uf; C0805
JP1: JUMPER-SMT_3_2-NC_TRACE_SILK; SMT-JUMPER_3_2-NC_TRACE_SILK
JP2: HEADER-1X4; 1X04_OVAL
JP3: JUMPER-SMT_2_NO_SILK; SMT-JUMPER_2_NO_SILK
R1, R2, R3: 4.7K; R0805
R4, R5: 100K; R0805
SJ1: SOLDERJUMPER_CLOSED; SOLDERJUMPER_CLOSEDWIRE
U2: CCS811; LGA10

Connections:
3.3V: C1.1, JP1.2, JP2.4, R2.2, R5.2, U2.6 (VDD)
!INT: !INT.TP, U2.3 (!INT!)
!RST: !RST.TP, R2.1, U2.2 (!RESET!)
!WAKE: !WAKE.TP, R4.2, U2.7 (!WAKE!)
AUX: U2.8 (AUX)
CCS811_ADDR: JP3.2, R5.1, U2.1 (ADDR)
GND: C1.2, JP2.3, JP3.1, SJ1.1, U2.EP (GND)
unnamed: R4.1, SJ1.2
unnamed: JP1.3, R3.2
unnamed: JP1.1, R1.2
NTC_SENSE: U2.4 (PWM), U2.5 (SENSE)
SCL: JP2.2, R1.1, U2.10 (SCL)
SDA: JP2.1, R3.1, U2.9 (SDA)

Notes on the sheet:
I2C address Open (Default) - 0x5B Closed - 0x5A
© 2020 AmbaSat Ltd Authors: John Mowbray, Martin Platt, Sudu Malli Web: ambasat.com

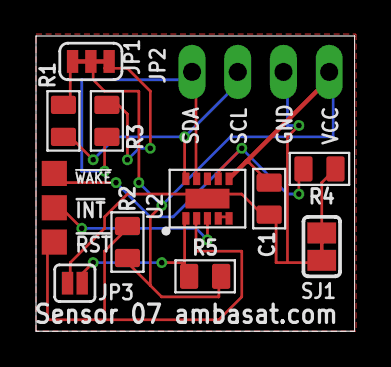
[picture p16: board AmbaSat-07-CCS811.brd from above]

Board: 2 copper layers, 17.7 x 16.4 mm, 14 parts (0 on the bottom side), 12 nets.

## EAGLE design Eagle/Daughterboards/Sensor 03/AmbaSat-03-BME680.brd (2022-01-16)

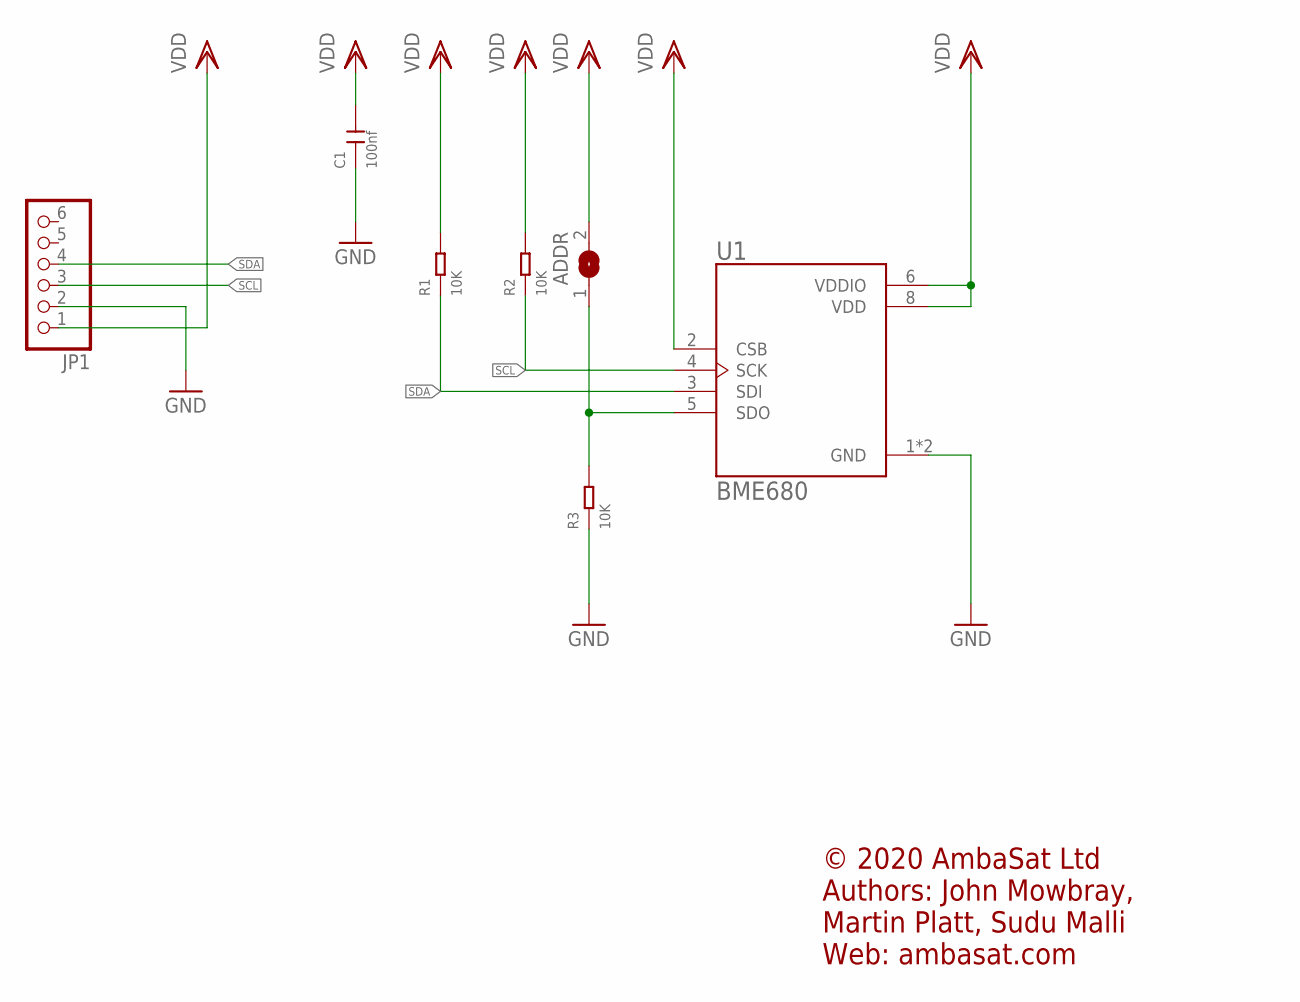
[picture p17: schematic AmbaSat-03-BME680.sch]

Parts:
ADDR: SJ
C1: 100nf; C0805
JP1: HEADER-1X6; 1X06_OVAL
R1, R2, R3: 10K; R0805
U1: BME680; PSON80P300X300X100-8N

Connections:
GND: C1.1, JP1.2, R3.1, U1.1 (GND), U1.7 (GND)
unnamed: ADDR.1, R3.2, U1.5 (SDO)
SCL: JP1.3, R2.1, U1.4 (SCK)
SDA: JP1.4, R1.1, U1.3 (SDI)
VDD: ADDR.2, C1.2, JP1.1, R1.2, R2.2, U1.2 (CSB), U1.6 (VDDIO), U1.8 (VDD)

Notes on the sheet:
© 2020 AmbaSat Ltd Authors: John Mowbray, Martin Platt, Sudu Malli Web: ambasat.com

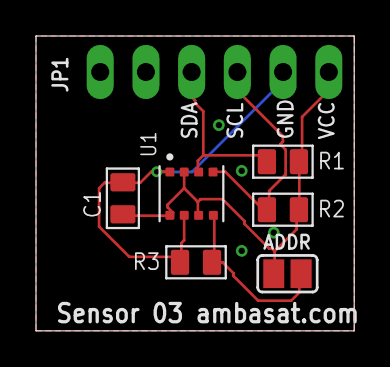
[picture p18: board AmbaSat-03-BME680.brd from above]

Board: 2 copper layers, 17.7 x 16.4 mm, 7 parts (0 on the bottom side), 5 nets.

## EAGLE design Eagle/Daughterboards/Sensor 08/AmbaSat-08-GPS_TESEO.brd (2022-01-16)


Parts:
C4: 10nf; C0805
C5, C6: 56pf; C0805; MPN CC0805FRNPO9BN560; DIGIKEY 311-4179-1-ND
C7: 1nf; C0805; MPN CC0805JRX7R9BB102; DIGIKEY 311-4270-1-ND
C8, C9: 120pf; C0402; MPN CC0402JRNPO9BN121
JP1: HEADER-1X6; 1X06_OVAL
L1: LQG15HS27NJ02D; LQG15HN2N2S02D; MPN LQG15HS27NJ02D; DIGIKEY_PART_NUMBER 490-2628-1-ND
L2: LQW15AN5N6C10D; LQG15HN2N2S02D; MPN LQW15AN5N6C10D; DIGIKEY_PART_NUMBER 490-6833-1-ND
R1: 10K; R0805
RST_N: TESTPAD_TPSQTP11SQ; TESTPAD_TP11SQ
RX: TESTPAD_TPSQTP11SQ; TESTPAD_TP11SQ
TX: TESTPAD_TPSQTP11SQ; TESTPAD_TP11SQ
U1: TESEO-LIV3F
U2: CGGBP.25.2.A.02; ANTENNA-PATCH
U3: BGA725L6; PSON35P100X100X35-6N
U4: B39162B4327P810; FIL_B39162B9417K610

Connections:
ANTOFF: R1.2, U1.13 (ANT_OFF), U3.6 (PON)
GND: C4.1, C5.1, C6.1, C7.1, JP1.5, R1.1, U1.1 (GND), U1.10 (GND_RF1), U1.12 (GND_RF2), U3.1 (GND), U3.4 (GNDRF), U4.2 (GND3), U4.3 (GND2), U4.5 (GND)
unnamed: RX.TP, U1.3 (RX)
unnamed: TX.TP, U1.2 (TX)
unnamed: C5.2, L1.1, U1.6 (VBAT), U1.7 (VCC_IO), U1.8 (VCC)
unnamed: RST_N.TP, U1.9 (!SYS_RST)
unnamed: L2.2, U3.5 (IN)
unnamed: C8.2, L2.1
unnamed: C9.1, U4.4 (OUT)
unnamed: C9.2, U1.11 (RF_IN)
unnamed: C8.1, U2.ANT
unnamed: U3.3 (OUT), U4.1 (IN)
SCL: JP1.4, U1.17 (SCL)
SDA: JP1.3, U1.16 (SDA)
VCC: C4.2, JP1.6, L1.2
VCC-ISO: C6.2, C7.2, U1.14 (VCC_RF), U3.2 (VCC)

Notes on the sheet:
© 2020 AmbaSat Ltd Authors: John Mowbray, Martin Platt, Sudu Malli Web: ambasat.com


Board: 2 copper layers, 26.6 x 30.1 mm, 17 parts (0 on the bottom side), 16 nets.

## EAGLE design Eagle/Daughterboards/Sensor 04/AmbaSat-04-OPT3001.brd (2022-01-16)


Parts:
1000100: SOLDERJUMPER_CLOSED; SOLDERJUMPER_CLOSEDWIRE
1000101, 1000110, 1000111: SJ
C1: 100nf; C0805
INT: TPTP11R; TP11R
JP1: HEADER-1X6; 1X06_OVAL
R1, R2, R3, R4*: 10K; R0805
U2: OPT3001; SON65P200X200X65-7N

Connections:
GND: 1000100.1, C1.1, JP1.5, U2.3 (GND), U2.7 (PAD)
INT: INT.TP, R3.1, U2.5 (INT)
unnamed: 1000101.2, R4*.1
unnamed: 1000100.2, 1000101.1, 1000110.1, 1000111.1, U2.2 (ADDR)
SCL: 1000111.2, JP1.4, R2.1, U2.4 (SCL)
SDA: 1000110.2, JP1.3, R1.1, U2.6 (SDA)
VDD: C1.2, JP1.6, R1.2, R2.2, R3.2, R4*.2, U2.1 (VDD)

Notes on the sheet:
You MUST connect only one at a time. Don't solder multiple jumper pads
Possible I 2C Addresses with Corresponding ADDR Configuration DEVICE I 2C ADDRESS ADDR PIN 1000100 > GND(default) 1000101 > VDD 1000110 > SDA 1000111 > SCL
Do not populate if you don't need this I2C address(1000101)
© 2020 AmbaSat Ltd Authors: John Mowbray, Martin Platt, Sudu Malli Web: ambasat.com


Board: 2 copper layers, 17.7 x 16.4 mm, 12 parts (0 on the bottom side), 7 nets.

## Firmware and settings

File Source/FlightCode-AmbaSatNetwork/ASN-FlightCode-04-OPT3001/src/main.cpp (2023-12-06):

/*******************************************************************************
* AmbaSat-1 
* Filename: main.cpp
* AmbaSat Network (ASN) Flight Code for Sensor 01 - SHT31: Temperature & Humidity
* 6th December 2023
*
* Copyright (c) 2023 AmbaSat Ltd
* https://ambasat.com
*
* licensed under Creative Commons Attribution-ShareAlike 3.0
* ******************************************************************************/

#include "main.h"
#include <Wire.h>
#include <ClosedCube_OPT3001.h>
#include "AmbaSatLSM9DS1.h"
#include <RH_RF95.h>

// The AmbaSat Network (ASN) *****************************  
// Network Session Key / DO NOT SHARE
static const PROGMEM uint8_t NWKSKEY[16] = {0x00,0x00,0x00,0x00,0x00,0x00,0x00,0x00,0x00,0x00,0x00,0x00,0x00,0x00,0x00,0x00};

// LoRaWAN AppSKey, application session key / DO NOT SHARE
static const uint8_t PROGMEM APPSKEY[16] = {0x00,0x00,0x00,0x00,0x00,0x00,0x00,0x00,0x00,0x00,0x00,0x00,0x00,0x00,0x00,0x00};

// AmbaSat Network end-device address (DevAddr) / DO NOT SHARE
static const uint32_t DEVADDR = 0x00000000 ;
/********************************/

int sleepcycles = 8; // eg. 8 x 8 secs = 64 secs sleep. 130 X 8 secs = ~17 mins sleep

// ============================================================================
void(* resetFunc) (void) = 0;  //declare reset function at address 0
void configureSensor() ;
void printError(String text, OPT3001_ErrorCode error);
void printResult(String text, OPT3001 result); 

ClosedCube_OPT3001 opt3001;
#define OPT3001_ADDRESS 0x44  // OPT3001 I2C address is 0x45(69)

// AmbaSat Library objects (see: https://platformio.org/lib/search?query=ambasat)
AmbaSatLSM9DS1 *ambasatLSM9DS1;

// RadioHead Library object
RH_RF95 radio(RFM95_CS, RFM95_INT);


// -----------------------------------------------------------------------------
// RFM95 setup
// -----------------------------------------------------------------------------
void radioSetup()
{
    pinMode(RFM95_RST, OUTPUT);
    digitalWrite(RFM95_RST, HIGH);

    // manual reset
    digitalWrite(RFM95_RST, LOW);
    delay(10);
    digitalWrite(RFM95_RST, HIGH);
    delay(10);

    while (!radio.init())
    {
        Serial.println("LoRa radio init failed");
        while (1);
    }

    RH_RF95::ModemConfig modem_config = {
      0x78, // Reg 0x1D: BW=125kHz, Coding=4/8, Header=explicit
      0xc4, // Reg 0x1E: Spread=4096chips/symbol, CRC=enable
      0x0c  // Reg 0x26: LowDataRate=On, Agc=On
    };
    
    radio.setModemRegisters(&modem_config);

    Serial.println("LoRa radio init OK");

    if (!radio.setFrequency(RF95_FREQ)) 
    {
        Serial.println("setFrequency failed");
    }

    radio.setTxPower(23, false);
    radio.sleep();
}

// ============================================================================

void setup()
{
    Serial.begin(9600);

    while (!Serial)
        delay(10);    

    // Turn the LED ON 
    pinMode(LED_PIN, OUTPUT);
    digitalWrite(LED_PIN, HIGH);

    // Create the sensor object

    opt3001.begin(OPT3001_ADDRESS);

    configureSensor();

    printResult("High-Limit", opt3001.readHighLimit());
    printResult("Low-Limit", opt3001.readLowLimit());
    Serial.println("----");          

    // Create the IMU object
    ambasatLSM9DS1 = new AmbaSatLSM9DS1();

    // Initialise IMU
    if (ambasatLSM9DS1->begin(LSM9DS1_AG, LSM9DS1_M) == false) 
    {
        PRINTLN_DEBUG(F("Failed to communicate with the AmbaSat-1 LSM9DS1 IMU"));
        while (1);
    }

    radioSetup();    

    PRINTLN_DEBUG("Setup complete");    
    // Turn the LED OFF
    digitalWrite(LED_PIN, LOW);    
}

// ============================================================================

void loop()
{
    uint16_t voltage;

    voltage = readVcc();

    OPT3001 result = opt3001.readResult();

    uint8_t voltsEncoded = (uint8_t) (voltage / 100);   // eg. 2840 millivolts becomes 28 and in the Dashboard decoded to 2.8 volts
 
    PRINT_DEBUG(F("LUX: "));
    PRINT_DEBUG(result.lux);   
    PRINT_DEBUG(F(", VOLT: "));
    PRINTLN_DEBUG(voltsEncoded);   

    // read LSM9DS1
    ambasatLSM9DS1->readGyro();
    ambasatLSM9DS1->readAccel();
    ambasatLSM9DS1->readMag();

    PRINT_DEBUG(F("GYRO: "));
    PRINT_DEBUG(ambasatLSM9DS1->gx);
    PRINT_DEBUG(F(", "));
    PRINT_DEBUG(ambasatLSM9DS1->gy);
    PRINT_DEBUG(F(", "));
    PRINTLN_DEBUG(ambasatLSM9DS1->gz);    

    PRINT_DEBUG(F("ACCEL: "));
    PRINT_DEBUG(ambasatLSM9DS1->ax);
    PRINT_DEBUG(F(", "));
    PRINT_DEBUG(ambasatLSM9DS1->ay);
    PRINT_DEBUG(F(", "));
    PRINTLN_DEBUG(ambasatLSM9DS1->az);      

    PRINT_DEBUG(F("MAG: "));
    PRINT_DEBUG(ambasatLSM9DS1->mx);
    PRINT_DEBUG(F(", "));
    PRINT_DEBUG(ambasatLSM9DS1->my);
    PRINT_DEBUG(F(", "));
    PRINTLN_DEBUG(ambasatLSM9DS1->mz);  
 

   /*
   // ***********************************************
   // GYRO DATA TO BE PROCESSED
    message.addUint16(ambasatLSM9DS1->gx); 
    message.addUint16(ambasatLSM9DS1->gy); 
    message.addUint16(ambasatLSM9DS1->gz); 
        
    message.addUint16(ambasatLSM9DS1->ax); 
    message.addUint16(ambasatLSM9DS1->ay); 
    message.addUint16(ambasatLSM9DS1->az); 

    message.addUint16(ambasatLSM9DS1->mx); 
    message.addUint16(ambasatLSM9DS1->my); 
    message.addUint16(ambasatLSM9DS1->mz); 
   // **********************************************
   */

    packetData.deviceId = DEVADDR;
    packetData.lux = result.lux;
    packetData.voltage = voltsEncoded;

    int radioBufLen = sizeof(packetData);

    uint8_t y = checksum( (unsigned char*)(&packetData), radioBufLen - 1);
    packetData.checksum = y;

    Serial.println("Checksum:" + String(packetData.checksum));
    Serial.print("Sending packet: ");
    PrintHex8( (uint8_t*)&packetData, radioBufLen);

    // Send it
    radio.setHeaderTo(GATEWAY_ID);
    radio.setHeaderFrom(SENSOR_ID);

    radio.send((const uint8_t*)(&packetData), radioBufLen);
        
    Serial.println("Packet sent, sleeping");
    radio.waitPacketSent(5000);

    radio.sleep();


    // sleep 8 seconds * sleepcycles
    for (int i=0; i < sleepcycles; i++)
    {
        LowPower.powerDown(SLEEP_8S, ADC_OFF, BOD_OFF);    
    }     

    resetFunc(); 
}

// ============================================================================

uint16_t readVcc()
{
    // Read 1.1V reference against AVcc
    // set the reference to Vcc and the measurement to the internal 1.1V reference
    #if defined(__AVR_ATmega32U4__) || defined(__AVR_ATmega1280__) || defined(__AVR_ATmega2560__)
        ADMUX = _BV(REFS0) | _BV(MUX4) | _BV(MUX3) | _BV(MUX2) | _BV(MUX1);
    #elif defined (__AVR_ATtiny24__) || defined(__AVR_ATtiny44__) || defined(__AVR_ATtiny84__)
        ADMUX = _BV(MUX5) | _BV(MUX0);
    #elif defined (__AVR_ATtiny25__) || defined(__AVR_ATtiny45__) || defined(__AVR_ATtiny85__)
        ADMUX = _BV(MUX3) | _BV(MUX2);
    #else
        ADMUX = _BV(REFS0) | _BV(MUX3) | _BV(MUX2) | _BV(MUX1);
    #endif

    delay(2); // Wait for Vref to settle
    ADCSRA |= _BV(ADSC); // Start conversion
    while (bit_is_set(ADCSRA,ADSC)); // measuring

    uint8_t low  = ADCL; // must read ADCL first - it then locks ADCH
    uint8_t high = ADCH; // unlocks both

    long result = (high<<8) | low;

    result = 1125300L / result;
    return result; // Vcc in millivolts
}

// ==============================================================================
void configureSensor() 
{
    OPT3001_Config newConfig;
    
    newConfig.RangeNumber = B1100;	
    newConfig.ConvertionTime = B0;
    newConfig.Latch = B1;
    newConfig.ModeOfConversionOperation = B11;

    OPT3001_ErrorCode errorConfig = opt3001.writeConfig(newConfig);
   
    if (errorConfig != NO_ERROR)
    {
        printError("OPT3001 configuration", errorConfig);
    }
    else 
    {
        OPT3001_Config sensorConfig = opt3001.readConfig();
        Serial.println("OPT3001 Current Config:");
        Serial.println("------------------------------");
        
        Serial.print("Conversion ready (R):");
        Serial.println(sensorConfig.ConversionReady,HEX);

        Serial.print("Conversion time (R/W):");
        Serial.println(sensorConfig.ConvertionTime, HEX);

        Serial.print("Fault count field (R/W):");
        Serial.println(sensorConfig.FaultCount, HEX);

        Serial.print("Flag high field (R-only):");
        Serial.println(sensorConfig.FlagHigh, HEX);

        Serial.print("Flag low field (R-only):");
        Serial.println(sensorConfig.FlagLow, HEX);

        Serial.print("Latch field (R/W):");
        Serial.println(sensorConfig.Latch, HEX);

        Serial.print("Mask exponent field (R/W):");
        Serial.println(sensorConfig.MaskExponent, HEX);

        Serial.print("Mode of conversion operation (R/W):");
        Serial.println(sensorConfig.ModeOfConversionOperation, HEX);

        Serial.print("Polarity field (R/W):");
        Serial.println(sensorConfig.Polarity, HEX);

        Serial.print("Overflow flag (R-only):");
        Serial.println(sensorConfig.OverflowFlag, HEX);

        Serial.print("Range number (R/W):");
        Serial.println(sensorConfig.RangeNumber, HEX);

        Serial.println("------------------------------");
    }    
}

// ==============================================================================
void printResult(String text, OPT3001 result) 
{
	if (result.error == NO_ERROR) 
  {
      Serial.print(text);
      Serial.print(": ");
      Serial.print(result.lux);
      Serial.println(" lux");
	}
	else 
  {
	  	printError(text,result.error);
	}
}

// ==============================================================================
void printError(String text, OPT3001_ErrorCode error) 
{
    Serial.print(text);
    Serial.print(": [ERROR] Code #");
    Serial.println(error);
}

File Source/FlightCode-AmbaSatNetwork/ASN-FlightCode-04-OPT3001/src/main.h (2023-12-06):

/*******************************************************************************
* AmbaSat-1 
* Filename: main.h
*
* Copyright (c) 2024 AmbaSat Ltd
* https://ambasat.com
*
* licensed under Creative Commons Attribution-ShareAlike 3.0
* ******************************************************************************
*
* Supporting code/libraries:
*
* LoRa code Copyright (c) 2015 Thomas Telkamp and Matthijs Kooijman
*
* Permission is hereby granted, free of charge, to anyone
* obtaining a copy of this document and accompanying files,
* to do whatever they want with them without any restriction,
* including, but not limited to, copying, modification and redistribution.
* NO WARRANTY OF ANY KIND IS PROVIDED.
**
*******************************************************************************/

#include <Arduino.h>
//#include <LoraMessage.h>
#include <Debugging.h>
#include "LowPower.h"

#define SERIAL_BAUD         9600 
#define LED_PIN             9

// AmbaSat-1 range of I2C compatible sensors and their TTN port IDs / Dashboard - config.inc
#define SENSOR_01_SHT31     51 // Temperature & Humidity
#define SENSOR_02_STS21     52 // Temperature
#define SENSOR_03_BME680    53 // Gas, Pressure, TVOC 
#define SENSOR_04_OPT3001   54 // Ambient Light
#define SENSOR_05_ZMOD4410  55 // TVOC 
#define SENSOR_06_SI1132    56 // UV 7 Ambient
#define SENSOR_07_CCS811B   57 // TVO & CO2
#define SENSOR_08_TESEO     58 // GPS

// LSM9DS1 Addresses
#define LSM9DS1_M	0x1E  // Mag address
#define LSM9DS1_AG	0x6B  // AG address

// -----------------------------------------------------------------------------
// Settings
// -----------------------------------------------------------------------------

// This Sensor ID, should be unique in the same network
#define SENSOR_ID       54     

// Gateway ID that will receive the messages from this node
#define GATEWAY_ID      1

// Network ID, only nodes from the same network see each other
#define NETWORKID       100

// Must match RX's freq!
#define RF95_FREQ       868.1

// The version number of the comms packet
#define PACKET_VERSION  1

// pins connected to Arduino (for reference, not required for Whisper Node)
#define RFM95_CS        10
#define RFM95_RST       9
#define RFM95_INT       2

#define LED_PIN         9

uint16_t readVcc();


// -----------------------------------------------------------------------------
// Transfer packet data structure
// -----------------------------------------------------------------------------
struct
{
      uint32_t deviceId;
      float lux; 
	  uint16_t voltage;
	  uint8_t checksum;
} packetData;


// -----------------------------------------------------------------------------
// Checksum calc
// -----------------------------------------------------------------------------
uint8_t checksum (unsigned char *ptr, size_t sz)
{
    uint8_t chk = 0;

    while (sz-- != 0)
    {
        chk -= *ptr++;
    }

    return chk;
}

// -----------------------------------------------------------------------------
// PrintHex8 - prints 8-bit data in hex with leading zeroes
// -----------------------------------------------------------------------------
void PrintHex8(uint8_t *data, uint8_t length)
{
    Serial.print("0x");

    for (int i=0; i<length; i++)
    {
        if (data[i]<0x10)
        {
           Serial.print("0");
        }

        Serial.print(data[i], HEX);
        Serial.print(" ");
    }

    Serial.print("\n");
}

// -----------------------------------------------------------------------------
// TTN payloads - see: https://www.thethingsnetwork.org/docs/devices/bytes.html
// -----------------------------------------------------------------------------

// TTN decode for OPT3001 is as below
//  
// 'voltage' - eg. 2840 millivolts becomes 28 and in the Dashboard is decoded to 2.8 volts
//
// AmbaSat 'SENSOR_04_OPT3001' TTN Payload Decoder expects:
// decode(bytes, [lux, uint8, uint8, int16, int16, int16, int16, int16, int16, int16, int16, int16], ['lux', 'humidity', 'voltage', 'gx', 'gy', 'gz', 'ax', 'ay', 'az', 'mx', 'my', 'mz']);

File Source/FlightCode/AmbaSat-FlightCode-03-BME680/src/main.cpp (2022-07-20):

/*******************************************************************************
* AmbaSat-1 
* Filename: main.cpp
* AmbaSat-1 Flight Code for Sensor 03 - BME680: Temperature, Humidty, Pressure,Gas
* 15th April 2022
* Authors: Martin Platt, James Vonteb 
* with contributions by Michael F. Kamprath, https://github.com/michaelkamprath
*
* Copyright (c) 2022 AmbaSat Ltd
* https://ambasat.com
*
* AmbaSat opensource code available on GitHub at:
* https://github.com/ambasat
*
* To use this code, set NWKSKEY, APPSKEY & DEVADDR values as per your Dashboard
* See the HowTo: https://ambasat.com/howto/kit-2/#/../unique-ids
*
* For ISM band configuration: See lmic/config.h eg. #define CFG_us915 1
* licensed under Creative Commons Attribution-ShareAlike 3.0
* ******************************************************************************/

#include "main.h"
#include "AmbaSatLMIC.h"
#include "AmbaSatLSM9DS1.h"
#include "AmbasatBME680.h"


void(* resetFunc) (void) = 0; // declare reset function at address 0


// TTN *****************************  
// The Network Session Key / DO NOT SHARE
static const PROGMEM u1_t NWKSKEY[16] = {0x00,0x00,0x00,0x00,0x00,0x00,0x00,0x00,0x00,0x00,0x00,0x00,0x00,0x00,0x00,0x00};

// LoRaWAN AppSKey, application session key / DO NOT SHARE
static const u1_t PROGMEM APPSKEY[16] = {0x00,0x00,0x00,0x00,0x00,0x00,0x00,0x00,0x00,0x00,0x00,0x00,0x00,0x00,0x00,0x00};

// LoRaWAN end-device address (DevAddr) / DO NOT SHARE
static const u4_t DEVADDR = 0x00000000;
/********************************/

int sleepcycles = 15; // 130 X 8 seconds = ~17 mins sleep

// AmbaSat Library objects (see: https://platformio.org/lib/search?query=ambasat)
AmbaSatLMIC *ambasatLMIC;
AmbaSatLSM9DS1 *ambasatLSM9DS1;
AmbasatBME680 *ambasatBME680;

// ============================================================================
// cppcheck-suppress unusedFunction 
void setup()
{
    Serial.begin(9600);

    while (!Serial)
        delay(10);    

    // Turn the LED ON 
    pinMode(LED_PIN, OUTPUT);
    digitalWrite(LED_PIN, HIGH);

    // Create the LMIC object
    ambasatLMIC = new AmbaSatLMIC();

    // Set static session parameters. Instead of dynamically establishing a session
    // by joining the network, precomputed session parameters are provided.
    uint8_t appskey[sizeof(APPSKEY)];
    uint8_t nwkskey[sizeof(NWKSKEY)];
    memcpy_P(appskey, APPSKEY, sizeof(APPSKEY));
    memcpy_P(nwkskey, NWKSKEY, sizeof(NWKSKEY));
    
    // Setup LMIC
    ambasatLMIC->setup(0x13, DEVADDR, appskey, nwkskey);

    ambasatBME680 = new AmbasatBME680();

    
    while(E_SUCCESS != ambasatBME680->begin())
	{
		Serial.print(F("-  Unable to find BME680. Trying again in 5 seconds.\n"));
		delay(5000);
        break;
	}
	while(E_SUCCESS != ambasatBME680->set_sensor(BME680_OS_8X,BME680_OS_2X,BME680_OS_4X,BME680_FILTER_SIZE_3,320,150))
	{
		Serial.print(F("-  Unable to configure BME680. Trying again in 5 seconds.\n")); 
		delay(5000);
        break;
	}
    
    // Create the IMU object
    ambasatLSM9DS1 = new AmbaSatLSM9DS1();

    // Initialise IMU
    if (ambasatLSM9DS1->begin(LSM9DS1_AG, LSM9DS1_M) == false) 
    {
        PRINTLN_DEBUG(F("Failed to communicate with the AmbaSat-1 LSM9DS1 IMU"));
        while (1);
    }

    // Turn the LED OFF
    digitalWrite(LED_PIN, LOW);
    PRINTLN_DEBUG("Setup complete");    
}

// ============================================================================

// cppcheck-suppress unusedFunction
void loop()
{
  
    uint16_t voltage;
    LoraMessage message;

    voltage = readVcc();
    
    PRINT_DEBUG(F("VOLT: "));
    PRINTLN_DEBUG(voltage);   
  
    uint8_t voltsEncoded = (uint8_t) (voltage / 100);   // eg. 2840 millivolts becomes 28 and in the Dashboard decoded to 2.8 volts

    // read LSM9DS1
    ambasatLSM9DS1->readGyro();
    ambasatLSM9DS1->readAccel();
    ambasatLSM9DS1->readMag();

    PRINT_DEBUG(F("GYRO: "));
    PRINT_DEBUG(ambasatLSM9DS1->gx);
    PRINT_DEBUG(F(", "));
    PRINT_DEBUG(ambasatLSM9DS1->gy);
    PRINT_DEBUG(F(", "));
    PRINTLN_DEBUG(ambasatLSM9DS1->gz);    

    PRINT_DEBUG(F("ACCEL: "));
    PRINT_DEBUG(ambasatLSM9DS1->ax);
    PRINT_DEBUG(F(", "));
    PRINT_DEBUG(ambasatLSM9DS1->ay);
    PRINT_DEBUG(F(", "));
    PRINTLN_DEBUG(ambasatLSM9DS1->az);      

    PRINT_DEBUG(F("MAG: "));
    PRINT_DEBUG(ambasatLSM9DS1->mx);
    PRINT_DEBUG(F(", "));
    PRINT_DEBUG(ambasatLSM9DS1->my);
    PRINT_DEBUG(F(", "));
    PRINTLN_DEBUG(ambasatLSM9DS1->mz);  
 
    // read bme680 data
    //REQUIRED TO GET ACCURATE DATA
    for( int i=0; i < 5;i++)
    {
        ambasatBME680->read_data();
        delay(2000);
    }
   // ***********************************************
   // Prepare message payload. NOTE: The order of the
   // payload data is important for the TTN decoder. 
   // Do not change the order
   // **********************************************    

    // TODO double check why values below are all zero
    message.addTemperature(float(ambasatBME680->field_data.temperature/100.0)); 
    message.addUint32(ambasatBME680->field_data.humidity/1000.0); 
    message.addUint32(ambasatBME680->field_data.pressure/100.0); 
    message.addUint32(ambasatBME680->field_data.gas_resistance/1000.0); 

    message.addUint8(voltsEncoded);

    message.addUint16(ambasatLSM9DS1->gx); 
    message.addUint16(ambasatLSM9DS1->gy); 
    message.addUint16(ambasatLSM9DS1->gz); 
        
    message.addUint16(ambasatLSM9DS1->ax); 
    message.addUint16(ambasatLSM9DS1->ay); 
    message.addUint16(ambasatLSM9DS1->az); 

    message.addUint16(ambasatLSM9DS1->mx); 
    message.addUint16(ambasatLSM9DS1->my); 
    message.addUint16(ambasatLSM9DS1->mz); 

    // send payload 
    ambasatLMIC->sendSensorPayload(SENSOR_03_BME680, message);  

    delay(3000);
    

    // sleep 8 seconds * sleepcycles
    for (int i=0; i < sleepcycles; i++)
    {
        LowPower.powerDown(SLEEP_8S, ADC_OFF, BOD_OFF);    
    }  

    resetFunc(); //call reset
       
}

// ============================================================================
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

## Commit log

2019-07-16 Create AmbaSat-1 BOM.xlsx
    BOM Added for Prototype
    [AmbaSat-1 BOM.xlsx]
2019-07-17 Adding updated BOM with designators and US links.
    [Ambasat1-v1-1-BOM.csv]
2019-08-21 C1 modification
    Value of C1 not displayed. Also incorrect. Was 1uF. Should be 0.1uF
    [AmbaSat-1 BOM.xlsx, AmbaSat-1v1-01-NO-solar.brd, AmbaSat-1v1-01-NO-solar.sch]
2019-10-12 AmbaSat-1 Motherboard and Solarboard release candidates
    AmbaSat-1 Motherboard (v.202) and Solarboard (v2.01) Release candidates
    [AmbaSat-1 version 2.0.brd, AmbaSat-1 version 2.0.sch, AmbaSat-1 version 2.01.brd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]
2019-10-12 AmbaSat-1 Sensor Datasheets
    Sensor datasheets for the 8 AmbaSat-1 sensor options
2019-10-14 Solarboard Design v2
    AmbaSat-1 solarboard gerber files
2019-10-14 AmbaSat-1 Mainboard Gerber
    Gerber files for v2.02 of the AmbaSat-1 Mainboard
2020-01-12 Identification label updates to solar board
    Added version, company and other label details to the solarboard
    [SolarBoard version 2.0.brd, SolarBoard version 2.0.sch]
2020-01-12 Update SolarBoard version 2.01.brd
    [SolarBoard version 2.01.brd]
2020-01-12 Label updates - Schematic
    [SolarBoard version 2.01.brd, SolarBoard version 2.01.sch]
2020-01-12 Update AmbaSat-1 version 2.02.sch
    [AmbaSat-1 version 2.02.sch]
2020-01-12 Update AmbaSat-1 version 2.02.brd
    [AmbaSat-1 version 2.02.brd]
2020-01-15 Create AmbaSat-1 board version 2.02.pdf
2020-01-21 Create AmbaSat-1 Satellite BOM.xlsx
    Initial revision - AmbaSat-1 Satellite Bill of Materials (BOM)
    [AmbaSat-1 Satellite BOM.xlsx]
2020-01-21 AmbaSat-1 Satellite create
    Consolidated Ambasat-1 mainboard versions
    [AmbaSat-1 Satellite.brd, AmbaSat-1 Satellite.sch]
2020-01-21 Removed version reference from filename
    [AmbaSat-1 version 2.0.brd, AmbaSat-1 version 2.0.sch, AmbaSat-1 version 2.01.brd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]
2020-01-21 Deleted versions
    [AmbaSat-1 version 2.0.brd, AmbaSat-1 version 2.0.sch, AmbaSat-1 version 2.01.brd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]
2020-01-28 Create AmbaSat-1 Satellite schematic.pdf
2020-02-06 Initial commit - Sensor Examples
    Sensor Examples - 01 to 04. Also, I2C scan and LED Flash
2020-07-04 Sensorboard BOMs
    BOM updates for sensor boards
    [Sensor-01-BOM.xlsx, Sensor-02-BOM.xlsx, Sensor-03-BOM.xlsx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]
2020-08-14 Default BME680 AmbaSat-1 I2C address added
    Set I2C address of BME680 to its default of 0x76
2020-08-20 Accelerometer, Gyroscope, Magnetometer
    Initial commit
2020-10-08 Initial commit - Sensor Examples
    Sensor 06 example code
2020-10-30 Workspace added
    I2C-Scan workspace added
2020-10-30 AmbaSat-1 LED workspace added
    AmbaSat-1 LED workspace added
2020-11-05 Create AmbaSat-Sensor-01-SHT30.code-workspace
2021-02-21 Flight Code for Sensor 01 - SHT31
    Includes library dependencies for LMIC, SHT31 & IMU
2021-02-22 Flight Code for Sensor 01 - STS21
2021-02-27 Flight Code for Sensor 06 - SI1132
2021-03-22 boards folder added
2021-03-22 boards definition added to project
2021-06-25 Flight Code for Sensor 03 - BME680
    Initial revision
2022-01-16 Repository Structure Changes
    Folder organisation changed - "Prototype" & "Release" folders removed. Minor source file updates.
    [AmbaSat-01-SHT3x-DIS.brd, AmbaSat-01-SHT3x-DIS.sch, AmbaSat-02-STS21.brd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]
2022-07-20 fix Sensor 3 flight code
    [main.cpp]
2023-03-12 Added AmbaSat board to project
2023-03-12 Added TVOC I2C address
2023-03-23 AmbaSat board added to workspace
2023-11-08 AmbaSat Network Sensor 01 initial commit
2023-11-10 Flightcode Sensor 03 - AmbaSat Network code
    AmbaSat Network (ASN) support for Sensor 03
2023-11-11 AmbaSat Network Sensor 06 initial commit
    Sensor 06 support for the AmbaSat Network
2023-11-14 AmbaSat Network Sensor 02 initial commit
2023-11-15 AmbaSat Network Sensor 07 initial commit
2023-12-06 AmbaSat Network Sensor 04 initial commit
2024-01-15 AmbaSat Network Sensor 05 initial commit

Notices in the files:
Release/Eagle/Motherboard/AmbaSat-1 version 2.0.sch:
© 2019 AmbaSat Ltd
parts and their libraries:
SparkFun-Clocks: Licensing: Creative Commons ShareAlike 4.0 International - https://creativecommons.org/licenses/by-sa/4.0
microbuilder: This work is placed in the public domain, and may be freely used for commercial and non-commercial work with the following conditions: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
